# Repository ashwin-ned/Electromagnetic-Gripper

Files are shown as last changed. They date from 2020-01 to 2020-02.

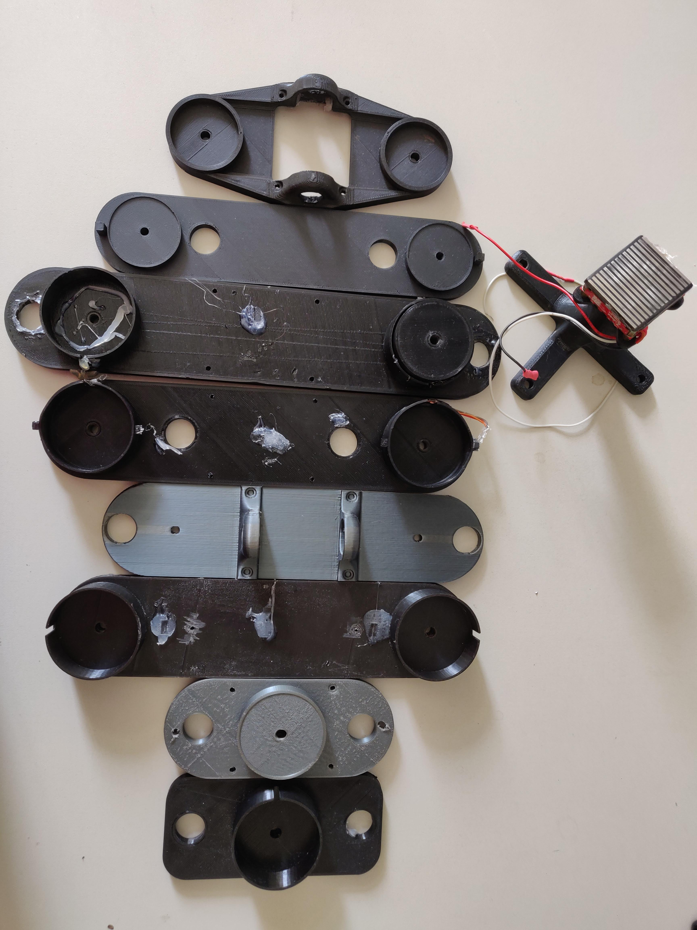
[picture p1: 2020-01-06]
videos/supplementry_media/B.Pictures/Tested_designs.jpg

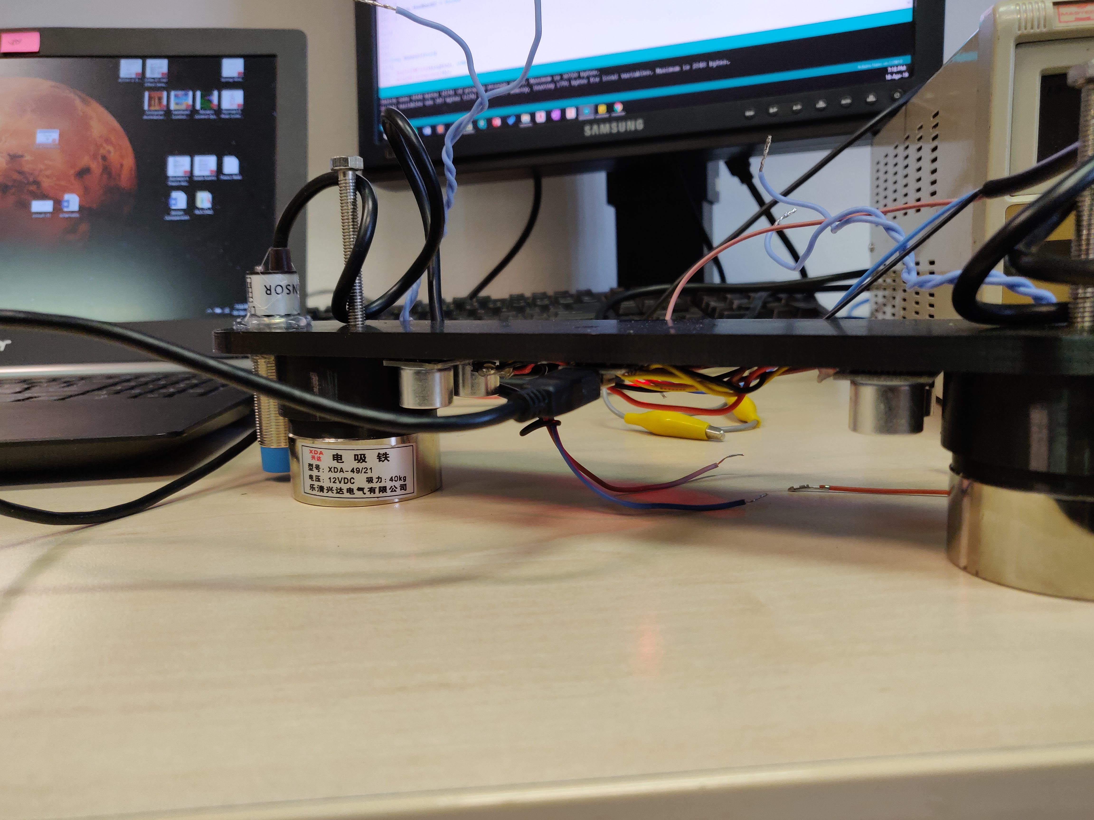
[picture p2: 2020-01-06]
videos/supplementry_media/B.Pictures/Ultrasonic_Test.jpg

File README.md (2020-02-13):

# Design of an Electromagnetic Gripper for Unmanned Aerial Vehicles (UAVs)
Source codes and media files from bachelor's thesis assignment **Design of an Electromagnetic Gripper for Unmanned Aerial Vehicles** with the Multi-Robot Systems Robotics group at Czech Technical University, Prague 2020. 

Note: The work was also accepted for publication in Springer's Lecture Notes in Computer Science under:
A Nedungadi and M Saska. “Design of an Active-Reliable Grasping Mechanism for Autonomous Unmanned Aerial Vehicles”. In Modelling and Simulation for Autonomous Systems (MESAS 2019). 

**Author = Ashwin Suresh Nedungadi** 

**Supervisor = Dr. Martin Saska, Ing.** 

**Website: http://mrs.felk.cvut.cz/**

**Year = 2020** 

**Thesis Topic = Design of an Electromagnetic Gripper for Unmanned Aerial Vehicles**

**Program = Bachelor's in Electrical Engineering & Computer Science [BEECS]**

**ABSTRACT**

This thesis work deals with the design of a grasping mechanism for
aerial grasping and assembly tasks by autonomous unmanned aerial
vehicles (UAVs). The proposed design is aimed at solving ferromagnetic
grasping by UAVs and has onboard sensors that detect and provide
reliable feedback to the UAV. The main focus of the work deals with
the design of the gripper, the technique used for feedback estimation and the integration of the entire mechanism into the current UAV systems at the MRS lab. Furthermore, an overview of the entire system and its implementation are discussed. The developed mechanism is tested multiple times under indoor and outdoor conditions and is designed to be deployed for Challenge II of the MBZIRC 2020 robotics competition in Abu Dhabi.

**Keywords:** unmanned aerial vehicle, aerial grasping, aerial object manipulation, sensor feedback

**Video of Experiments:**

Autonomous grasping test: https://youtu.be/WBgUNp1UqlA

Piloted grasping test: https://youtu.be/bOQ2FRhOzXw

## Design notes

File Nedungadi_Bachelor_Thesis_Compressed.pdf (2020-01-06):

## CZECH TECHNICAL UNIVERSITY IN PRAGUE

## Faculty of Electrical Engineering

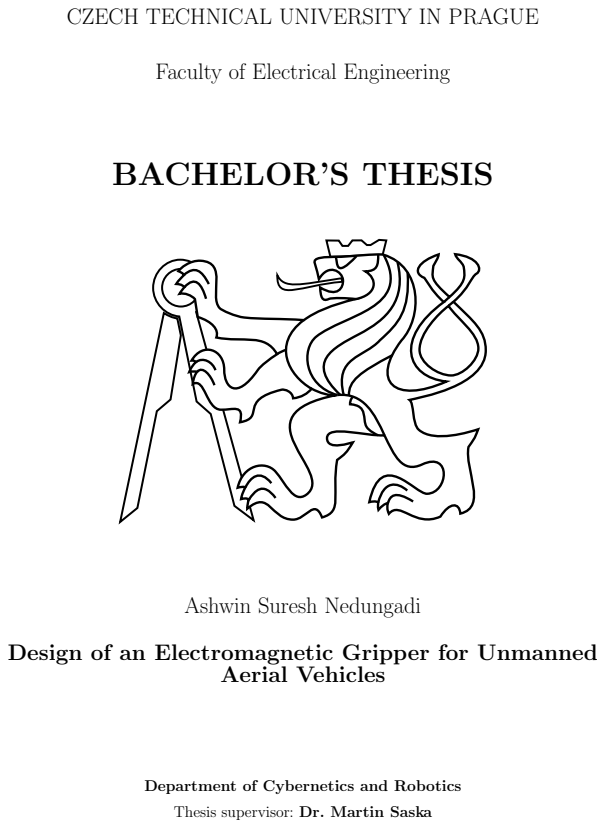
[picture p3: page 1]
BACHELOR’S THESIS; Aerial Vehicles

Ashwin Suresh Nedungadi

Design of an Electromagnetic Gripper for Unmanned

Department of Cybernetics and Robotics
Thesis supervisor: Dr. Martin Saska

# BACHELOR‘S THESIS ASSIGNMENT

I. Personal and study details
Student's name: | Nedungadi Ashwin Suresh | Personal ID number: | 464315
Faculty / Institute: | Faculty of Electrical Engineering

Department / Institute: Department of Cybernetics

Study program: Electrical Engineering and Computer Science

II. Bachelor’s thesis details

Bachelor’s thesis title in English:

Design of an electromagnetic gripper for unmanned aerial vehicles

Bachelor’s thesis title in Czech:

Návrh elektromagnetického uchytovače pro bezpilotní helikoptéry

Guidelines:

The goal of the thesis is to design, implement and experimentally verify a magnetic gripper for construction of a wall by unmanned aerial vehicles (UAV). The task is motivated by the second challenge of the MBZIRC 2020 competition, https://www.mbzirc.com/challenge/2020.
1) Design the magnetic gripper and measure its performance with real test bricks for the MBZIRC Competition.
2) Design and experimentally verify a feedback system for the magnetic gripper using range finder and/or Hall sensors.
3) Develop and Integrate a feedback system, then estimate the feedback status through ROS into the system of Multi-Robot Systems group at CTU.
4) Testing and evaluation of the gripper in the laboratory and field testing with the complete system onboard the drone.

Bibliography / sources:

[1] V Spurny, T Baca, M Saska, R Penicka, T Krajnik, J Thomas, D Thakur, G Loianno and V Kumar. Cooperative Autonomous Search, Grasping and Delivering in a Treasure Hunt Scenario by a Team of UAVs. Accepted in Journal of Field Robotics, 2018.
[2] LaValle, S. M.. Planning Algorithms. Cambridge University Press, Cambridge, U.K., 2006.

Name and workplace of bachelor’s thesis supervisor:

Ing. Martin Saska, Dr. rer. nat., Multi-robot Systems, FEE

Name and workplace of second bachelor’s thesis supervisor or consultant:

Date of bachelor’s thesis assignment: __________ Deadline for bachelor thesis submission: __________

Assignment valid until:
by the end of summer semester 2019/2020
___________________________ | ___________________________ | ___________________________ prof. Ing. Pavel Ripka, CSc. Dean’s signature
doc. Ing. Tomáš Svoboda, Ph.D.
Head of department’s signature

Ing. Martin Saska, Dr. rer. nat.
Supervisor’s signature

III. Assignment receipt

The student acknowledges that the bachelor’s thesis is an individual work. The student must produce his thesis without the assistance of others,
with the exception of provided consultations. Within the bachelor’s thesis, the author must state the names of consultants and include a list of references.
Date of assignment receipt | Student’s signature
CVUT-CZ-ZBP-2015.1 | © ČVUT v Praze, Design: ČVUT v Praze, VIC

i

## Declaration of Independent Work

I declare that the presented work was done independently and that I have listed all sources of information used within it in accordance with the methodical instructions for observing the ethical principles in the preparation of an university thesis.

In Prague on | | |

ii

# Acknowledgements

I would like to thank my supervisor Dr. Martin Saska for his support and guidance during this project. I would also like to thank my advisor Ing. Daniel Heˇrt for his valuable inputs and for teaching me something about hardware. Furthermore, I would like to thank all the members of the Multi-Robot Systems group for their help with the outdoor experiments and for letting me be part of the team.
Finally, I would like to express my gratitude toward my parents who have shown incredible support, love, and encouragement during my studies.

iv

v

### Abstract

This thesis work deals with the design of a grasping mechanism for aerial grasping and assembly tasks by autonomous unmanned aerial vehicles (UAVs). The proposed design is aimed at solving ferromagnetic grasping by UAVs and has onboard sensors that detect and provide reliable feedback to the UAV. The main focus of the work deals with the design of the gripper, the technique used for feedback estimation and the integration of the entire mechanism into the current UAV systems at the MRS lab. Furthermore, an overview of the entire system and its implementation are discussed. The developed mechanism is tested multiple times under indoor and outdoor conditions and is designed to be deployed for Challenge II of the MBZIRC 2020 robotics competition in Abu Dhabi.

Keywords: unmanned aerial vehicle, aerial grasping, aerial object manipulation, sensor feedback

vi

# Contents

List of Figures | ix
List of Tables | xi
1 Introduction | 1
2 Preliminaries | 9
3 Description of the Gripper | 19

viii | Contents
4 Feedback and Control | 31
5 Outdoor Experiments | 43
6 Conclusion | 51
Bibliography | 53
Appendices | 59
Appendix List of abbreviations | 63

# List of Figures

1.1 Example of a UAV with onboard instruments, GPS antenna and battery . 2

1.2 A UAV attempts to grasp a dynamically moving item on top of a turtle bot while another UAV transports the already grasped item to the drop zone
(MBZRIC 2017) | | 4
2.1 Diagram of how communication between nodes work in ROS | | 10
2.2 The variation of magnetic field and flux with thickness of surface | | 12
2.3 Working principle of an ultrasonic sensor | | 13
2.4 Working principle of an inductive proximity sensor | | 14
2.5 Working principle of a hall-effect sensor | | 14
2.6 Free body diagram of UAV with coupled payload | | 15
2.7 Forces acting on a UAV in forward flight | | 16
2.8 Manufactured test bricks | | 17
3.1 Gripper used for MBZRIC 2017 | | 21
3.2 Gripper prototype with ultrasonic sensors and onboard MCU | | 22
3.3 The dual-grasping gripper during test flight | | 22
3.4 Experimental manual flights with onboard gripper prototype | | 23
3.5 Prototype of the rigid gripper with embedded hall-sensors and MCU . . . . | 24

3.6 Modeled CAD assembly of proposed gripper showing 1. Electromagnet, 2.
Gripper housing, 3. Sensors used for feedback, 4. Arduino MCU | | 25
3.7 Modules of the gripper | | 27
3.8 All mechanical components of the gripper | | 28
3.9 Comparison between the previous gripper and proposed gripper | | 29
3.10 Side by side comparison of the grippers in outdoor test flights | | 30

x | List of Figures
4.1 HC-SR04 ultrasonic sensor | | 32
4.2 Feedback algorithm using ultrasonic sensors | | 33
4.3 Unfiltered distance data from ultrasonic sensor during test flight | | 34
4.4 Median filtered distance data from ultrasonic sensor during test flight . . . | 34
4.5 Hall sensors embedded in the electromagnet surface | | 35
4.6 The used inductive proximity sensor | | 36
4.7 Raw data from Hall-Effect sensor and feedback during test flight | | 37
4.8 Raw data from Inductive proximity sensor and feedback during test flight . | 37

4.9 Combined data from proximity & hall sensor and feedback during test flight 38

4.10 Algorithm running onboard the MCU and high level processes | | 39
4.11 Electrical schematic of the gripper circuit | | 40
4.12 Description of the serial protocol | | 41
5.1 Hardware architecture | | 44
5.2 Overview of software pipeline | | 45
5.3 Sub-Pipeline for autonomous grasping | | 46
5.4 The complete system in action during outdoor experimental flights | | 47

5.5 Snaps from outdoor experiments where the complete system is tested under
the challenge II scenario | | 49
5.6 UAV positional control during grasping of brick | | 50
5.7 Control error during grasping of brick | | 50

# List of Tables

2.1 Parameters of tested bricks | | 17
3.1 Comparison between the tested gripping systems | | 29
4.1 Serial bits and their function in used protocol | | 42
4.2 Implemented functions facilitated by ROS | | 42
5.1 Test of maximum slide force | | 48
1 | CD Content | | 61
2 | Lists of abbreviations | | 63

xii | List of Tables

# Chapter 1

# Introduction

### Contents

Unmanned aerial vehicles (UAVs) or Multi-Rotor Systems (Fig. 1.1) that are capable of vertical take-off and landing (VTOL) have undergone a revolutionary advancement in the past few years. They are being used for a wide range of applications in the consumer and technological sector from film making and photography, transportation [1][2][3] and autonomous delivery, hobby products and hobby flying to military applications [4][5] such as defense and reconnaissance systems. UAVs, with on board equipment are also ideal platforms for research [6][7][8] particularly in the areas of disaster relief, search and rescue as well as exploration [9][10] due to their low cost, small size and the variety of configurations in which they can be built.

These vehicles typically consist of 4 (quad-copters) or more rotors with fixed pitch propellers that are driven by brushless DC motors which together, produce thrust for the aircraft. By varying the thrust generated by the individual motors using ESCs (electronic speed controllers), the UAV can pitch, roll and yaw in a given direction.

With the improvement of hardware technologies and their growing applications, UAVs are being used in more complex tasks where interaction and manipulation with the environment are necessary, thus creating an increasing demand for the development of grasping mechanisms that can reliably lift, transport and manipulate objects.

### 2 Chapter 1. Introduction

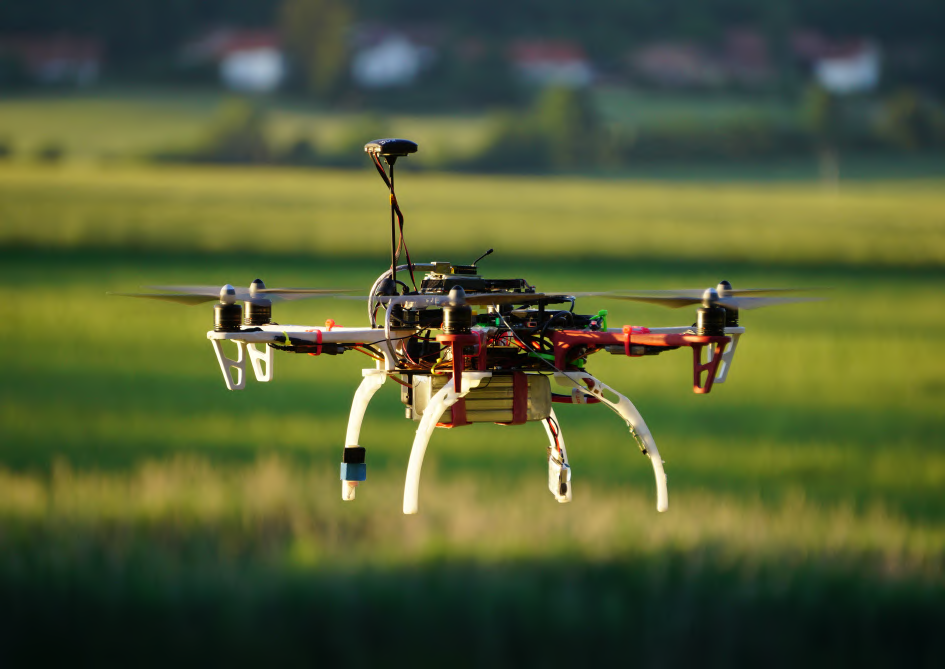
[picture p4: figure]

Figure 1.1: Example of a UAV with onboard instruments, GPS antenna and battery

There are however, many challenges in such aerial grasping tasks as rotor aircraft are inherently susceptible to strong gusts of wind and disturbances during hover making the control of such UAVs a challenge. Other problems include limited payload capabilities of the UAV itself and flight stability with payload coupling as the attached payload changes the flight dynamics compared to free flight.
Moreover, the grasped object should be aligned with the center of mass of the UAV without which, the stability of the UAV is uncertain during transportation of the payload which may induce abnormal maneuvers or oscillations to the UAV, resulting in a crash.

The required grippers for such aerial tasks have to be robust mechanically and must be able to be controlled reliably by a pilot or the autonomous system onboard. They should also stay light-weight and draw the minimum power from the UAV’s battery source to be used in practice.
For aerial grasping or autonomous transportation tasks, the designed gripper must be able to lift a variety of payloads and also be able to provide reliable feedback on the status of the said payload under outdoor conditions.
This thesis deals with the design and verification of a robust electromagnetic based grasping mechanism with a system for reliable feedback of the grasped object for autonomous aerial grasping and manipulation tasks for the upcoming MBZIRC 2020 robotics competition (Sec. 1.3.1).
The thesis work takes an iterative R&D approach, testing and refining various designs over multiple iterations. The design of the grasping mechanism, the approach used to estimate feedback using various sensors and the overall system is described in the following pages.

1.1. Problem statement | 3

## 1.1 Problem statement

The primary objective of this thesis is to design and experimentally verify an electromagnetic grasping mechanism with suitable feedback to be used in an assembly task by a group of UAVs using a range of bricks with different masses and sizes and deploy it for the second challenge of the MBZIRC 2020 competition.
The designed gripper system is then integrated within the UAV system with control and feedback in ROS (Robot operating system). Furthermore, we provide an overall description of the current systems in development for the MBZIRC 2020 competition along with the analysis of the data from the designed gripper during different outdoor experimental tests.

## 1.2 Structure of this thesis and contribution

This thesis work is structured into 6 main chapters as follows:

- The first chapter gives an introduction to the problem, the challenge and source of inspiration and also discusses related works in detail. Most of the cited research works focus on the topics related to the theme of this thesis.
- In the second chapter we establish some preliminary conditions and discuss various principles necessary to fully understand the problem and solution design.
- In chapters 3 and 4, we provide the description and design of the proposed grasping mechanism, the algorithms and also include certain high level and low level aspects of the system.
- In chapter 5 we present the description of the overall UAV system as well as experimental data from test flights followed by some analysis and discussion of the experiments, and in chapter 6 finally we conclude the work.

This thesis contributes directly to the research done for the MBZIRC project where we present [11] a novel idea for an electromagnetic grasping mechanism that can lift theoretical payloads of up-to 6 kg. The designed gripper is robust and can lift a range of ferromagnetic payloads from small loads of 100 g to 6 kg. The designed gripper is thoroughly tested in multiple outdoor experiments and through iterative design refined into a final prototype to be used for the competition.

### 4 Chapter 1. Introduction

## 1.3 MBZIRC competition

The Mohamed Bin Zayed International Robotics Challenge (MBZIRC) [12] is an international robotics competition that is held every two years in Abu Dhabi, United Arab Emirates and comprises of various demanding challenges in which the best university teams in the world compete in attempts to solve the challenges (Fig. 1.2) for maximum amount of points.

The objective of the MBZIRC competition is to provide an ambitious and technologically demanding set of challenges in robotics intended to demonstrate the current state of the art in robotics in terms of scientific and technological accomplishments, and to inspire the future of robotics.

In the MBZIRC 2017 competition, the team led by Multi-Robot Systems group from Czech Technical University won various prizes in the different challenges presented. The team comprised of 20 members as a part of a larger collaboration effort between the University of Pennsylvania, University of Lincoln.
The most notable and relevant prize won by the team to this thesis was the first place in the third challenge where a group of 3 UAVs had to locate and retrieve circular metallic disks and drop them in a defined drop zone in a “Treasure Hunt” scenario. This thesis builds upon the lessons learnt from the MBZIRC 2017 experience and contributes towards the upcoming MBZRIC 2020 competition.

Figure 1.2: A UAV attempts to grasp a dynamically moving item on top of a turtle bot while another UAV transports the already grasped item to the drop zone (MBZRIC 2017)

1.4. State of the art | 5

### 1.3.1 MBZIRC 2020

The next MBZIRC competition is scheduled for February of 2020 in Abu Dhabi with over 30 international teams competing for the prizes. MBZIRC 2020 will be based on autonomous aerial and ground robots, carrying out navigation and manipulation tasks under harsh indoor and outdoor conditions.
MBZIRC 2020 will consist of three individual challenges and a triathlon type Grand Challenge which is a combination of the first three challenges. The challenges will be focused in the areas of UAV tracking & interaction, construction automation and urban fire-fighting:
- In challenge I, the first task requires a team of UAVs to autonomously detect, track and eliminate a set of balloons in an open field, the second task requires a UAV to chase and catch a ball that is being transported by another UAV. Challenge I is motivated by precise detection and elimination tasks by UAVs and UAV safety.
- In challenge II, a team of 3 UAVs along with a UGV (unmanned ground vehicle) detect, grasp, transport and assemble different types of bricks into a pre-defined structure in an outdoor environment. This challenge is motivated by autonomous construction using robots.
- In challenge III, the same team comprising of 3 UAVs and a UGV is required to work cooperatively to extinguish a series of simulated fires in a building structure under an urban fire-fighting scenario.
- In the final Grand Challenge, the team of autonomous robots work together to attempt to solve all the 3 challenges simultaneously in a timed event.

## 1.4 State of the art

There are several available solutions for aerial grasping. Many of which focus on passive magnetic grasping and robotic claw like manipulators for the grasping or aerial manipulation of objects. We will discuss each of the various techniques proposed and their advantages and disadvantages for aerial grasping tasks.

One such example of a solution for aerial grasping includes work done by the RISC laboratory at King Abdullah university of science and technology [13] where a passive magnetic gripper with an impulse release mechanism and push-button feedback was developed. The design uses 16 small neodymium magnets which together produce the required magnetic force to grasp a ferromagnetic object. The release of the grasped object is facilitated by two high speed servos which pushes the drop plate and produces a high impulse release of the object.
While this kind of grasping mechanism provides a low-power passive solution, the grasping

### 6 Chapter 1. Introduction

capabilities provided by permanent magnets are inferior compared to that of an electromagnet in terms of magnetic strength and control. Furthermore, the release mechanism that relies on servomotors to separate the grasped object with impulse is bulky and adds another layer of unnecessary complexity to the system.
A scaled up version of this concept was also developed by the KAIST team [14] for MBZIRC 2017 competition. The system integrated contact sensors and 2 camera modules on the gripper for visual servoing and used 13 neodymium magnets and 4 servomotors that actuated the drop plate to forcefully separate the grasped object from the gripper.

Another popular solution for magnetic grasping utilizes electro-permanant magnets (EPMs) due to their low-power consumption (table 3.1), payload capabilities and ability to toggle the magnetic strength by magnetizing and demagnetizing the EPM with the help of an active external switching circuit.
This solution was used by several teams, including our own team in the 2017 MBZRIC competition using the COTS¹ OpenGrab EPM V3 from nicadrone [15][16][17].
A custom EPM based solution was also presented in the work [18] by ETH Zurich which has the ability to grasp ferromagnetic objects with a curvature of up to 30 degrees and utilizes alnico and neodymium magnets. Another custom solution was tested in the MRS lab for cooperative grasping by UAVs in the master’s thesis work [19] which used servomotors to rotate neodymium magnets by 90 degrees for grasp and release.
Although electro-permanent solutions are popular candidates for aerial grasping and manipulation tasks and offer low-power solutions, they come with many disadvantages. They are expensive, do not scale well with mass, have low payload capabilities and require an active control circuit to magnetize and demagnetize the magnet. Furthermore, there is a need for firm contact with the ferrous surface in order to grasp the object successfully. Moreover, as experienced by our team [16] and other teams [15][17] during the last MBZIRC 2017 competition, the magnet can also break if used with heavy force and the circuitry can burn out if the command signal is sent multiple times resulting in many gripper failures and an overall low success rate [17]. The teams also found that the EPM solution provided to be too weak in outdoor conditions where gripper failure was even caused due to the thick layer of paint on the objects in the competition [15][16][17].

There exists several unique ideas for aerial grasping developed over the years such as impactive or claw based, ingressive grasping techniques and suction based grasping. Impactive grasping mechanisms that are modeled after claws or human arms are widely studied problems in robotics. They are also used by industrial robots as end effectors for various automation tasks. Over the years there have been several publications regarding these mechanisms[20][21][22] each optimized for a specific task with it’s own set of advantages and disadvantages. Although such mechanisms offer a robust solution to grasp a wide range of objects with different shapes, they are far too complex and heavy to be used onboard UAVs. However, there are many existing simplified grasping mechanisms [23][21]

1Commercial off-the-shelf

1.4. State of the art | 7

and they have been proven to be suitable for grasping of wooden blocks and packages. But considering the requirements for the MBZIRC 2020 competition and the engineering complexity of developing such a mechanism, we had to eliminate such grasping techniques. Moreover, under a competitive scenario it is crucial that the hardware engineers are able to quickly debug and resolve any issues that could arise and having a complex system onboard multiple UAVs would be more of a liability to our team than a strength.

Two unique solutions for aerial grasping are presented in the works [24][25]. The first being a self-healing suction mechanism that utilizes an onboard vacuum pump that produces the sufficient volume flow to grasp a variety of payloads. Although the possibility of using suction for aerial grasping proves to be a great solution for non-magnetic object grasping and grasping of items with small curvature, the disadvantage of having a big enough compressor for heavy payloads and sufficient volume flow onboard the UAV combined with its complexity made it a clearly unsuitable candidate for our task.
The other grasping mechanism for aerial grasping utilizes an ingressive gripper. The mechanism consists of metallic “claws” or “hooks” driven by servo motors which penetrate the surface of the object to be grasped and hooks itself into the surface, allowing the UAV to carry the object. The hooks are then retracted using the servo motors when the UAV needs to release the object.
Such a mechanism is very useful as demonstrated in the work [25], to transport wooden blocks or packages with strong cardboard linings. However, it is impractical when it comes to rigid or delicate objects as it relies on penetrating the surface to grasp and makes an indent in the process which in the long term proves to be impractical and especially unsuitable for our task as the objects we want to grasp will be metal.

While the above mentioned aerial grasping solutions are not as simple or heavy payload compatible, our solution is designed for ferrous payloads and provides reliable feedback using multiple sensors on whether an object is successfully grasped or not. Moreover, electromagnets provide the solid advantage of scalability to the system while being cheap and can be hot swapped on the field to accommodate heavier or lighter payloads or in case of failure. The mechanical design of our gripper is developed with reliability and operation in outdoor desert conditions in mind while being able to lift ferrous objects weighing theoretically up to 6 kg with the only limitation being the payload capacity of the UAV used.

### 8 Chapter 1. Introduction

# Chapter 2

# Preliminaries

### Contents

In order to proceed with the rest of the thesis work, we need to establish some knowledge of the working principles involved. This chapter gives a brief introduction to the physical concepts and theory involved.

## 2.1 Robot Operating System (ROS)

ROS [26] is an open-source, meta operating-system running on Unix-based platforms and is widely used by the robotics community.

It provides the services expected from an operating system, including hardware abstraction, low-level device control, implementation of commonly-used functionality, message-passing between processes, and package management. It also provides various tools and libraries for obtaining, building, writing, and running code across multiple computers.
The basis of ROS is made up of packages, where all the software are located in the form of executable and supporting files.

A node in ROS is a process that performs some computation. Nodes in ROS can receive or publish messages known as “topics” to other nodes in a distributed manner. A robotic

### 10 Chapter 2. Preliminaries

system usually comprises of many nodes each of which does a specific task. For example, one node controls a laser range-finder, one node controls the thrust inputs to a controller, one node performs path planning, one node publishes diagnostics about a running process, and so on. Nodes can also call upon other nodes to do a specific task in the form of ROS services. ROS services are bi-directional messages and expect a reply from the receiving end.

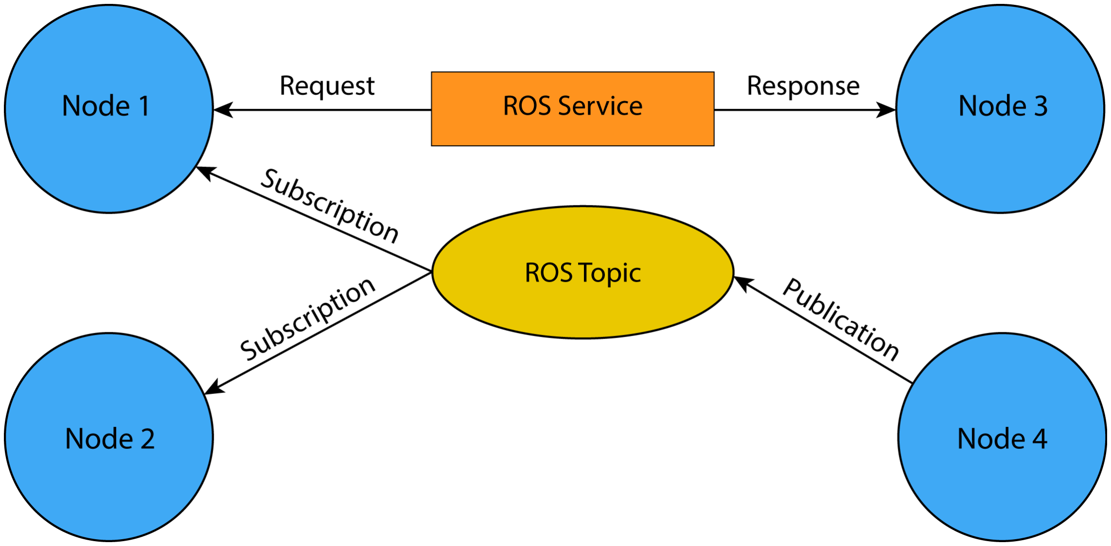
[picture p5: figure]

Figure 2.1: Diagram of how communication between nodes work in ROS

A ROS distribution is a versioned set of ROS packages. These are akin to Linux distributions (e.g. Ubuntu). The purpose of the ROS distributions is to let developers work against a relatively stable codebase until they are ready to roll everything forward.
Various distributions of ROS are used in the robotics community, the latest being Lunar Loggerhead. We however use Melodic Morenia for the purpose of our tasks.

## 2.2 Concepts of Electromagnetism

An electromagnet is a device consisting of a core of soft magnetic material¹
surrounded by
a coil through which an electric current is passed to magnetize the core. By definition, this means that an electromagnet can be turned on and off by passing current through it’s coil making it highly suitable for a wide range of applications.

Engineering an electromagnet is systematized by known equations that characterize a magnetic circuit and which decide certain properties of the designed electromagnet such

1Soft magnetic materials are those materials that are easily magnetised and demagnetised. They do not retain their magnetism after the electric current is removed.

2.2. Concepts of Electromagnetism | 11

as holding force.
The holding force of an electromagnet is defined as the force which is perpendicular to the attraction surface of the holding magnet.
The force exerted by a magnetic field or the holding force of an electromagnet is described by the equation:

Fh =

B²A
2µo
, | (2.1)

for a closed magnetic circuit with no air gap:

B =

NIµ
L
. | (2.2)

Where B is the magnetic flux density; A is the cross sectional area of the core; N is the number of turns of coil winding; I the current in the winding coil and L, the length of the magnetic field path.
The constants µ and µo being the permeability of the electromagnet core material and permeability of free space respectively.

Substituting (Eq. 2.2) into (Eq. 2.1), we get the relationship for the holding force of an electromagnet:

Fh =

N²
I

2µ

2A
2µoL²
. | (2.3)

Electromagnets are also subject to side effects, some of which that must be discussed here as they will become relevant later [27][28][29].

1. Power losses due to Ohmic heating: In electromagnets, it is common for energy to dissipate as heat due to the resistance of the windings which scales proportionally as the size of the electromagnet begins to increase.
Electromagnets come in various thermal insulation classes, which is categorized by a limiting temperature beyond which the performance of the electromagnet will be affected²
The ohmic heating effect can be reduced by limiting the current in the coils or using thicker coils to decrease their resistance.
2. Inductive voltage spikes during disconnection: Electromagnets have significant inductance which resists changes in the current through its windings, sudden changes in the winding current causes large voltage spikes across the windings.
This is because when the current through the magnet is increased, such as when it is turned on, energy from the circuit is stored in the magnetic field. When it is turned off the energy in the field is returned to the circuit. Thus, when an electromagnet is disconnected, the energy in the magnetic field is suddenly returned to the circuit, causing a large voltage spike and an arc across the switch contacts. The electrical

2The magnet used in this project has an insulation class of B (130⁰ C)

### 12 Chapter 2. Preliminaries

circuits involving electromagnets usually counter this problem with the help of a “freewheeling diode” or “fly back diode” [30] connected across the electromagnet. Large electromagnets avoid this by using power circuits controlled by a microprocessor that achieves current changes slowly, in gentle ramps taking several minutes to energize or deenergize the magnet.

3. Remanence effect: Remanence or residual magnetic field [31][32] is the magnetization left behind in a ferromagnetic material after the external magnetizing field is removed. This effect is known to occur in electromagnets causing the payload to be attached to it even after the electromagnet has been turned off. This problem can be countered by a process known as degaussing or in our case, a quick polarity change of the electromagnet voltage.
4. Variation of holding force as a function of surface thickness: From our earlier equation (Eq. 2.1), the holding force of a magnet is characterized by the square of it’s flux density [33]. Hence, the holding force of an electromagnet relies on the thickness of the part to be held.
The thicker the target surface is, the greater the number of magnetic field lines passing through the object (Fig. 2.2 from [28]). Therefore, if the part to be held is too thin then it will not be able to accommodate all the available field lines and will become saturated. The force will then be inadequate and the electromagnet will be unable to hold on to such a thin surface.

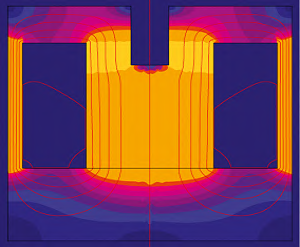
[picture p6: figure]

(a) Surface of thickness 0.2 mm | (b) Surface of thickness 10 mm

Figure 2.2: The variation of magnetic field and flux with thickness of surface

2.3. Sensors used and working principles | 13

## 2.3 Sensors used and working principles

A few different types of sensors were considered for the feedback of whether a brick was successfully grasped or not as this was a critical task for autonomous grasping. We will look into the principles of their working.

### Distance Sensing with Ultrasonic Sensor

Ultrasonic sensors work by emitting sound waves at a high frequency then wait for the sound to be reflected back, calculating distance based on the total time (Fig. 2.3 from [34]). This is similar to how radar measures the time it takes a radio wave to return after hitting an object. For this reason an ultrasonic sensor has an ultrasonic emitter and receiver.
We know the elementary formula Distance = Speed ∗ T ime, thus by measuring the time taken by an ultrasonic wave to be reflected off an object and detected up the sensor again, we can formulate:
d = c.

1
2
t | (2.4)

where d is distance and is given by the product of c - speed of sound in air at room temperature (≈ 343 m/s) and t - the total transmission time.

Figure 2.3: Working principle of an ultrasonic sensor

### Distance Sensing with Inductive Proximity Sensor

Inductive proximity sensors are non-contact measurement devices used in detection of metallic objects. Their operating principle is based on a coil and oscillator that creates an oscillating electromagnetic field in the close surroundings of the sensing surface (Fig. 2.4 from [35]). The presence of a metallic object in the operating area causes a dampening of the oscillation amplitude due to energy loss by induced eddy currents in the metallic object.
The rise or fall of such oscillation is identified by a threshold circuit that changes the output of the sensor. In the sensor used for this thesis³
, this threshold was at 2 mm distance from the sensor.

3The sensor used is the LJ8A3-2-Z Inductive Proximity Sensor with sensing capability of upto 2 mm.

### 14 Chapter 2. Preliminaries

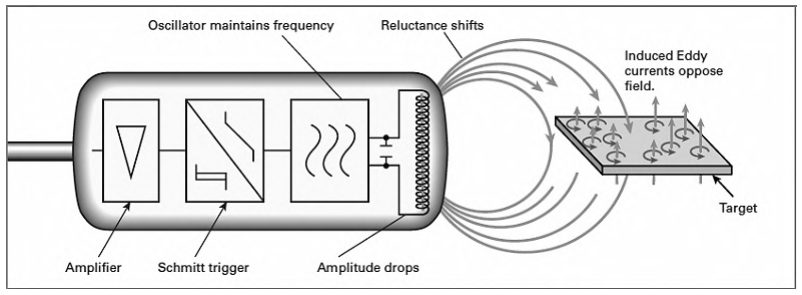
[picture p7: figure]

Figure 2.4: Working principle of an inductive proximity sensor

### Magnetic Sensing with Hall-Effect Sensor

A Hall effect sensor is a device that is used to measure the magnitude of a magnetic field (Fig. 2.5 from [36]). Its output voltage is directly proportional to the magnetic field strength through it.
Hall effect⁴
sensors are used in various areas to measure position, speed, and magnetic field. The principle of semiconductor hall sensors is that when a current-carrying semiconductor is introduced to a magnetic field, the charge carriers of the semiconductor experience a force in a direction perpendicular to both the magnetic field and the current⁵ and hence a voltage appears at the semiconductor edges.

Figure 2.5: Working principle of a hall-effect sensor

4The sensor used is a linear hall effect sensor SS49e 5As per Fleming’s right hand rule

2.4. Forces acting on a UAV with coupled payload | 15

## 2.4 Forces acting on a UAV with coupled payload

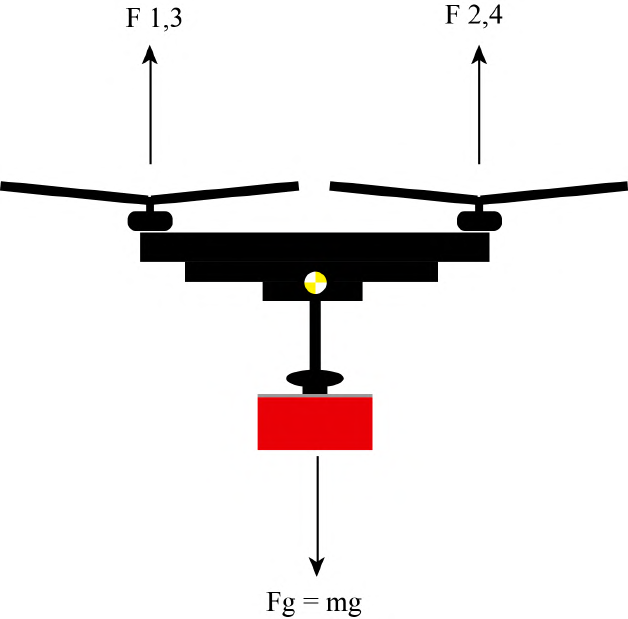
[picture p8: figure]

Figure 2.6: Free body diagram of UAV with coupled payload

The forces acting on the UAV [37] behaves differently based on if a payload is attached rigidly or can move about some axes. In the case of rigid mechanics, There is a force acting downward (Fig. 2.6) F~
g = m~g which needs to be compensated by the collective thrust produced by the UAV F~

c = F~

1 + F~

2 + F~

3 + F~

4. The thrust force F~
i of a rotor can be given
by the formula:
F~
i = Kf ω

2
(2.5)

Where ω is the rate of rotation of the propellers and Kf is a proportionality constant that depends upon many factors like torque proportionality constant, back-EMF, Density of surrounding air, area swept by propeller etc. and is measured empirically.
At equilibrium (hover condition), the collective thrust generated by a quadrotor balances out the weight of the drone as:

X

4

i=1

Kf ωi

2 + m~g = 0 | (2.6)

But suppose the thrust is more than the mass, in this case the quadrotor accelerates upward and the equation is given by:

X

4

i=1

Kf ωi

2 + m~g = m~a | (2.7)

### 16 Chapter 2. Preliminaries

Figure 2.7: Forces acting on a UAV in forward flight

A UAV in flight, is acted upon by four basic aerodynamic (Fig. 2.7) forces [38]:

1. Lift: Lift is the force that opposes the downward force of weight and is produced as a result of the motion of the propellers through air [39]. It depends on factors such as speed of airflow, density of air, area and pitch of the used propellers. For a quad-copter, the maximum lift produced is fixed due to the fixed pitch propellers and maximum rpm (revolutions per minute) generated by each motor.
2. Weight: Weight is the combined load of the UAV itself, including the instruments, air-frame, payload and battery. It pulls the UAV downward due to the force of gravity and opposes lift vertically in the opposite direction through the center of gravity. In most cases, the weight of the UAV is fixed and known.
3. Thrust: The force produced by the rotors is called thrust. It can be forward, rearward, sideways or vertical. The UAV attitude and thrust determines the direction of movement of the UAV.
4. Drag: The drag force is a rearward, retarding force caused by wind resistance and disruption of airflow by the rotor, air-frame and payload. It opposes thrust.

In the case of a coupled payload, a certain degree of freedom can complement the UAV’s ability to carry and transport the payload while reducing mechanical stress and strains on the grasping or suspension mechanism. However, a new problem arises where the disturbances during flight cause the coupled payload to swing around like a pendulum. This problem is widely studied [40][41] but cannot be easily overcome in the real world without the proper position and orientation feedback of the payload and the aerodynamic interactions due to the downward airflow from the UAV.

2.5. Parameters of tested bricks | 17

## 2.5 Parameters of tested bricks

To simulate the correct conditions for our outdoor experiments, it was necessary to manufacture and test our systems on the proposed bricks from the MBZRIC 2020 organizers. A complete list of the challenge criteria and parameters of the objects involved can be found online [12].
The manufactured test bricks used Styrofoam, adhesive and metal sheets of various thick-
ness providing the necessary mass for the proposed bricks⁶ | . Multiple bricks were manufac-
tured with the heaviest variant being 4 kg (blue) and the lightest being 0.75 kg (red). The tested bricks and their parameters are shown in table 2.1.
Brick Color | Dimensions | Mass
Red | 0.30 m x 0.20 m x 0.20 m | 0.75 kg - 1.0 kg
Green | 0.60 m x 0.20 m x 0.20 m | 1.40 kg - 2.0 kg
Blue | 1.20 m x 0.20 m x 0.20 m | 2.36 kg - 4.0 kg

Table 2.1: Parameters of tested bricks

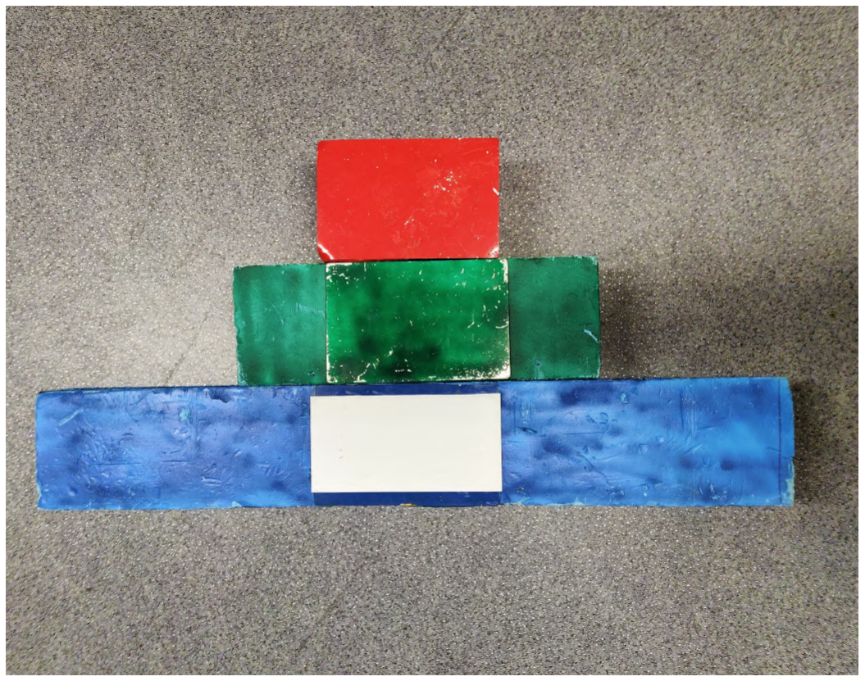
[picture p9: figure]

Figure 2.8: Manufactured test bricks

6The manufactured bricks were made to be worst case scenarios of the described parameters from MBZIRC 2020, hence they exceeded the competition requirements.

### 18 Chapter 2. Preliminaries

# Chapter 3

# Description of the Gripper

### Contents

Aerial grasping and manipulation is a well known problem in the field of modern aerial robotics. They are also highly desirable capabilities that an unmanned aerial vehicle can possess.
In most cases however, commercial based aerial grasping mechanisms such as magnetic or suction-based end effectors designed for industrial robots, are not suitable for autonomous aerial operation or robust enough to be employed so. Therefore, custom designed grasping mechanisms are often favored because the current state of the art in 3D printing technology makes it accessible to rapidly prototype such custom solutions and the fact that they can be customized for specific applications and adapted on the field makes it an ideal choice for research and development.

The designed grippers for aerial manipulation and transportation tasks must be engineered to be mechanically robust and compliant while considering the following requirements:

- Lightweight
- Sufficient holding force for payload
- Low power consumption
- Autonomous control and reliable feedback

### 20 Chapter 3. Description of the Gripper

- Fail-safe grasp and release

A viable aerial grasping mechanism will have to fullfill the above conditions to be used onboard an autonomous UAV in outdoor conditions.

## 3.1 Tested Iterations

Following the methodology for iterative designing, we have tested multiple prototypes for a suitable electromagnetic grasping mechanism while rejecting bad designs and reinforcing promising ones through trial and error.

### EPM based solution

The gripper (Fig. 3.1) used for MBZIRC 2017 [16] consisted of an Electro-Permanent Magnet (EPM) end effector attached to a ball joint that could freely rotate in all directions and a compression spring along the shaft that connects it to the UAV.
Although this worked well for the task described by the competition (Sec. 1.3), several groups who participated (Sec. 1.4) experienced problems with the EPM based solution [15][17] including our team from CTU.

The primary problem was the burning of the control circuit on the OpenGrab V3 EPM when the command signal for activation is sent multiple times as this was done to strengthen the holding force after an object was initially grasped. Secondly, the EPM is very delicate for outdoor environments as dirt or gravel could be crushed into the surface causing an insulation breakdown [42]. Furthermore, it provided to be weak in terms of holding force as it only had 15 kg of holding force which was effectively reduced it to 2.25 kg in shear [16] and even lower considering the forces acting on it during flight [38].

Another problem encountered by our team was due to the design of the mechanical ball joint which had unlimited freedom in the yaw axis, which meant that any object grasped in flight would yaw along the directions of the acting forces and considering that the competition took place near the sea and was affected by strong sea breezes, this became problematic.
Since the next competition requires UAVs to transport long cuboidal bricks, a ball joint would be highly undesirable due to the uncontrollable yawing motion caused by the different forces on the payload in flight [38].
Considering all the above problems it was decided to abandon any EPM based solution for the next MBZIRC as the objects described were bigger and have masses upward of 1 kg.

3.1. Tested Iterations | 21

Figure 3.1: Gripper used for MBZRIC 2017

### Dual electromagnets with ultrasonic-hall feedback

While going through the design process for the gripper, it was crucial to come up with a design that was capable of grasping and transporting the proposed long brick-like objects in challenge II (Sec. 1.3.1).
Our hold force and power requirements were satisfied by a single electromagnet which had dimensions of 49/21 mm and was capable of lifting up to 40 kg under ideal conditions. The problem then is to take into consideration that the longest brick to be grasped was 1.2 m long and weighed 1.5 kg. For such a long brick, the placement of two electromagnets of lifting power 40 kg each separated by a distance of 20 cm was ideal¹ as the gripper would experience fewer torque effects (Fig. 3.3). As the challenge is timed, it is important to transport the bricks as fast as possible without causing disturbances to the payload or UAV. Hence, by grasping the brick at 2 positions, the drone could fly faster safely. The

1The separating distance of 20 cm was chosen as it was the right distance to accommodate even the smallest brick which was 0.3 m long

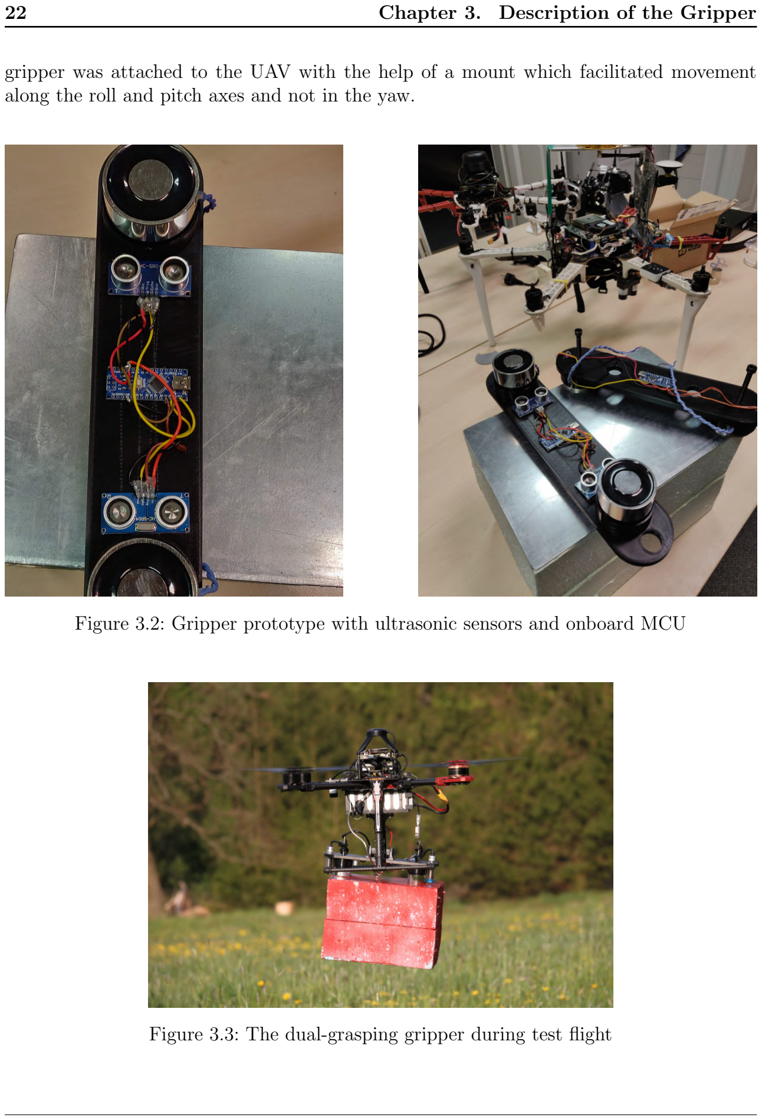
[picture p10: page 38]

### 22 Chapter 3. Description of the Gripper

gripper was attached to the UAV with the help of a mount which facilitated movement along the roll and pitch axes and not in the yaw.

Figure 3.2: Gripper prototype with ultrasonic sensors and onboard MCU

Figure 3.3: The dual-grasping gripper during test flight

3.1. Tested Iterations | 23

During the preliminary tests (Fig. 3.4), three prototypes of the gripper were tested, one with dual ultrasonic feedback (Fig. 3.2); the second with feedback from hall effect sensors: and finally a prototype that combined the ultrasonic sensors with proximity sensors to calculate total feedback of the gripper. The signal processing for feedback from each prototype is discussed in the next chapter.

Although by the design of the 2-DOF mount, the mechanism was able to align the grasped brick to the center of gravity (Fig. 3.3), there was a major drawback with the prototype. The long design of the dual grasping mechanism meant extra unnecessary weight, redundant sensors and twice the power consumption by the two electromagnets which translated to limited operating time before the batteries had to be changed. Moreover, due to the longer design, the gripper exhibited unstable “see-saw” like motion during flight when there was no payload due to the slight variation of forces acting on either ends due to downwash generated by the propellers and wind.
Due to the above reasons and due to the fact that there was a clear trade-off between the electromagnet’s hold force and power consumption, there was a need to simplify and miniaturize the design.

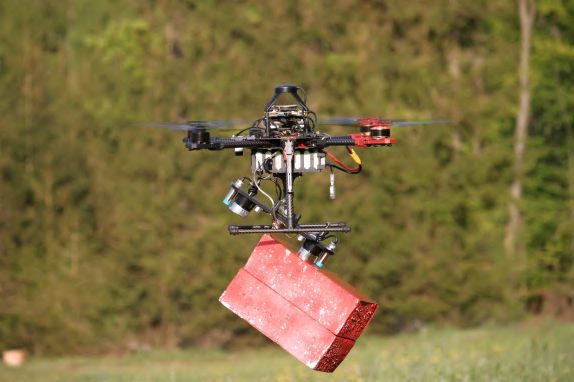
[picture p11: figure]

(a) The UAV in flight without payload | (b) Gripper with partial grasping of brick

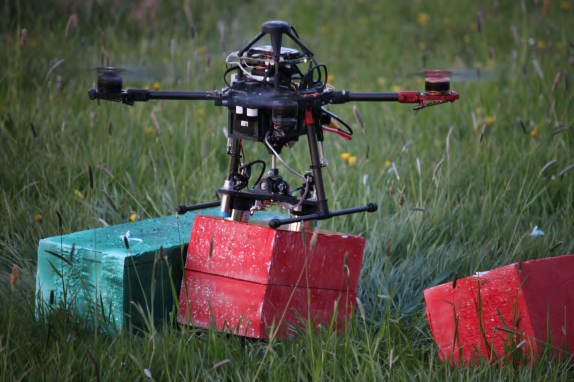
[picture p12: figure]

(c) UAV in front of wall structure | (d) UAV attempts to place a brick

Figure 3.4: Experimental manual flights with onboard gripper prototype

### 24 Chapter 3. Description of the Gripper

### Rigid Gripper

Another prototype proposed and tested by the MRS Lab was the idea of a solid gripper with a linear array of electromagnets that can grasp the brick horizontally. This prototype consisted of two smaller electromagnets of 25 kg holding force each and had hall sensors embedded on their surfaces for feedback. The base would attach via a solid compression shaft that is completely rigid and 3D printed as shown in Fig. 3.5.

While the solid design offers good brick placement for building a wall, such a design is not very robust as the forces during flight will act on the payload coupled UAV and cause high drag and mechanical strain on the gripper itself as well as decrease the hold force of the magnets [16]. To compensate for this, the UAV’s maneuvers and speed have to be severely restricted so that the brick does not fall down during transportation. Moreover, high quality of the 3D print has to be ensured without which, the base would fracture from the shear forces of flight.

(a) Side view showing the MCU, the compression shaft and mounting for the UAV

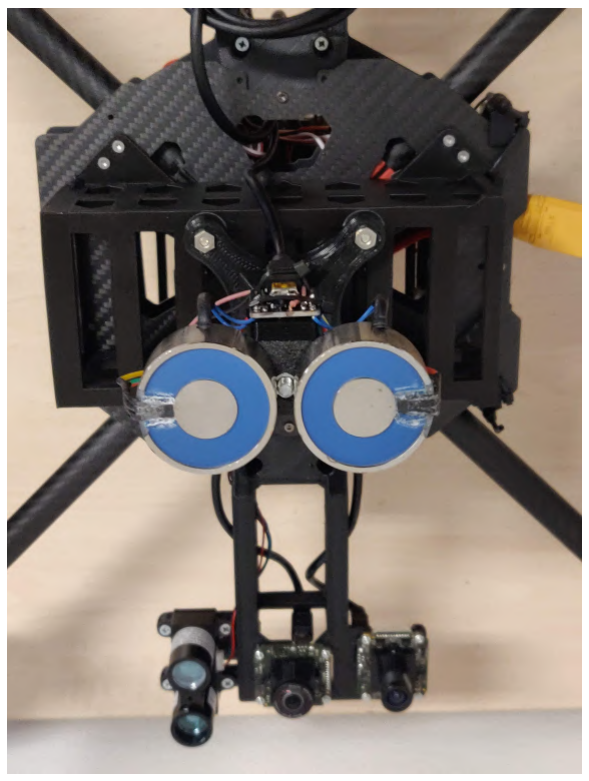
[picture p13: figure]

(b) Bottom view showing the embedded hall sensors on the electromagnet surface

Figure 3.5: Prototype of the rigid gripper with embedded hall-sensors and MCU

3.2. Proposed gripper design | 25

## 3.2 Proposed gripper design

The current proposed design of the gripper consists of 4 major components:

1. An electromagnet with switching circuit
2. Gripper housing with compression shaft and mounting attachment
3. A combination of a hall-effect sensor embedded in the electromagnet and inductive proximity sensor for feedback
4. Arduino MCU that processes raw signals from the sensors, communicates with the on-board computer and also controls the switching circuit of the gripper.

Figure 3.6: Modeled CAD assembly of proposed gripper showing 1. Electromagnet, 2. Gripper housing, 3. Sensors used for feedback, 4. Arduino MCU

### 26 Chapter 3. Description of the Gripper

### Electromagnet and switching circuit

An industrial electromagnet capable of lifting up-to 40 kg of payload provides the necessary magnetic hold force for grasping. The electromagnet is supplied a constant 12 V DC for its operation and has a custom built N-MOSFET switching circuit integrated with the Arduino that can be toggled by the UAV’s onboard computer (Sec. 2.1). Although the electromagnet consumes 10 W, it is insignificant compared to the power drawn by the UAV’s onboard computer (60 W) and motors (1000 W) from the 8000 mAh ( 178 Wh) Li-Po Battery. And considering the magnets won’t be turned on and in operation continuously throughout the flight, there is no particular reason to be concerned by the electromagnet’s power consumption.

### Gripper housing and mount

The gripper base (Fig. 3.7a) and mounting bracket is designed to be sturdy structurally and is fabricated using 3D printing technology with PLA and ABS plastic.
It has 2 degrees of freedom in the pitch and roll axes and consists of a main mount where the sensors, magnet and MCU are fixed, an inner and outer ring structure with ball bearings (Fig. 3.7c) to facilitate the movement along the two described axes and a shaft with a mounting bracket so it can be attached to the UAV with 4 screws and nuts (Fig. 3.7b) (Fig. 3.7d). By the mechanical design of the gripper, the angle of rotation for the 2 axes are restricted to approximately 30 degrees, this ensures that the grasped object does not swing too much and cause a disturbance for the drone.

### Feedback sensors and signal processing

Reliably estimating the status of a successful grasp is a crucial task for aerial autonomous grasping. The gripper integrates feedback from two independent sensors: A hall sensor embedded in the electromagnet’s surface and an inductive proximity sensor mounted on the side. The raw analog signal is first digitized by the Arduino’s 10-bit ADC (analog-digital converter) and is then processed using an algorithm and a final feedback is given using a combination of the feedback from the individual sensors.

The chosen MCU for prototyping the gripper is an Arduino nano as it is low-power (≈ 0.1 W), open-source and easy to program in the Arduino IDE. It also has 8 analog pins with a 10-Bit ADC for acquiring signals as well as 22 digital I/O pins which makes it very convenient to use in rapid prototyping.
The electronic components of the gripper consist of the electromagnet, N-Mosfet, Arduino nano MCU, hall-effect sensor and an inductive sensor.

3.3. Modeling & Assembly | 27

## 3.3 Modeling & Assembly

The gripper was modeled using Autodesk Fusion 360 CAD software and consists of 5 basic 3D printed modules shown in Fig. 3.7:

(a) The gripper base with holes for the proximity sensor and electromagnet with embedded hall sensor

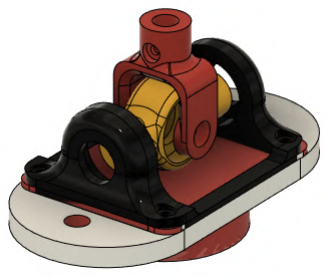
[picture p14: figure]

(b) The mount that connects the upper portion of the gripper with the base (black)
(c) Housing that connects the shaft to the base and housing that accommodates ball bearings and attaches to the gripper and together provides 2-DOF

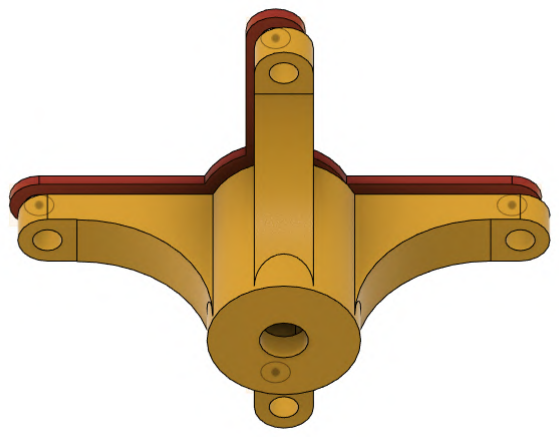
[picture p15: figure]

(d) The mount with spring for dampening and which connects to the UAV

Figure 3.7: Modules of the gripper

### 28 Chapter 3. Description of the Gripper

The gripper has a few components (Sec. 3.2) including sensors and MCU which can be assembled or soldered to each other by hand and assembled together to the 3D printed parts (1-5) by using some screws, nuts and short cylindrical²
inserts (a-g).
All the components and the final assembled product are shown in (3.8)(3.9).

Figure 3.8: All mechanical components of the gripper

2a - ball bearings; b - a metal rod with hex end; c - compression spring; d - cylindrical inserts; e -threaded bolt; f - M6 screw; g - two nuts

3.4. Comparison of tested prototypes | 29

## 3.4 Comparison of tested prototypes

Parameter | EPM Design | Dual Design | Rigid Design | Proposed Design
Weight | 250 g | 580 g | 350 g | 400 g
Max Rated Payload | 15 kg | 80 kg | 50 kg | 40 kg
Max Shear Payload | 2.25 kg | 12 kg | 7.5 kg | 6 kg
Max Tested Payload | 500 g | 1.5 kg | 2.3 kg | 4 kg
Feedback | Single | Multiple | Single | Multiple
Scalable | No | Yes | Yes | Yes
Mechanical Design | 3-DOF | 2-DOF | 0-DOF | 2-DOF
Power Consumption | ≈ 100 mW | ≈ 23 W | ≈ 20 W | ≈ 11.65 W
Cost | ≈ 146 Euros | ≈ 35 Euros | ≈ 15 Euros | ≈ 20 Euros

Table 3.1: Comparison between the tested gripping systems

From the comparison table 3.1, we can observe that the optimal grasping mechanism in terms of hold strength vs. power consumption is the proposed 2-DOF gripper design as its payload requirements meet our criterion in the context of the MBZIRC 2020 challenge (Sec. 1.3.1).
The mechanical design of the gripper is reasonable and does not contain any unnecessary elements that add to the weight. The power consumption, though is greater than the EPM solution, is reasonable considering the decreased cost and increased grasping strength and is significantly lower than the power consumption of the UAV.

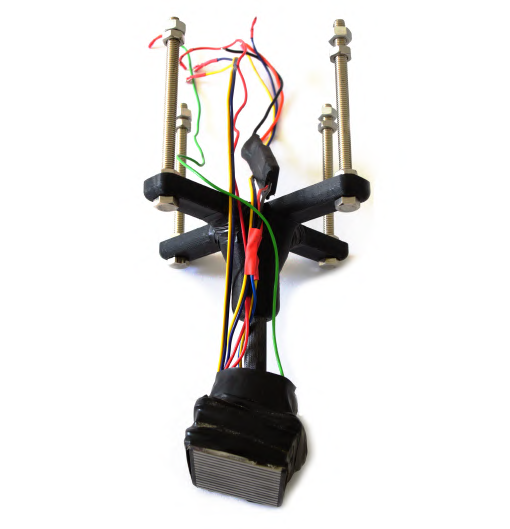
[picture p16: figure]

(a) gripper used for MBZIRC 2017 | (b) proposed gripper for MBZIRC
| 2020

Figure 3.9: Comparison between the previous gripper and proposed gripper

### 30 Chapter 3. Description of the Gripper

(a) Previously used EPM gripper grasping a 0.5 kg metal disk
(b) Proposed gripper grasping a 1.6 kg brick

Figure 3.10: Side by side comparison of the grippers in outdoor test flights

# Chapter 4

# Feedback and Control

### Contents

Reliably detecting whether a payload is actually grasped and onboard the UAV is one of the most crucial tasks for aerial grasping and manipulation.
There have been numerous works where the information about such payload coupling is estimated through the control of the drone wherein the controller detects the increase in the mass of the UAV system and compensates for this mass by varying thrust. Additionally, it is also possible to compensate for a swinging payload under the UAV and stabilize it through the controller [40][43][41]. This method however, becomes more challenging as the payload mass starts to become comparable with the UAV’s mass while considering that the UAV must actually grasp the brick for the controller to estimate the mass gradually and requires fine tuning to be practical enough to be employed in time constrained scenarios.

For our task, it is critical to know whether the brick has been successfully grasped almost immediately as the UAV has to fly the payload to the wall area without delay.
In case the grasp was unsuccessful, the UAV must try again to grasp the brick or decide to abandon the brick altogether. These decisions will be made on a higher level by a state machine that runs in the UAV’s onboard computer (Sec. 5.1). We shall discuss various sensing and estimation techniques for feedback to explore all possibilities and choose the optimal one for the purposes of our task.

### 32 Chapter 4. Feedback and Control

## 4.1 Feedback with ultrasonic sensors

The first sensor tested was the HC-SR04 ultrasonic sensor (Fig. 4.1 from [44]) with sensing range of 2 cm - 4 m and sensing accuracy of ± 3 mm¹
. Two sensors were tested with the first gripper prototype which had a longer body and hence was mounted on the sides of the long body as shown in Fig. 3.2.
The ultrasonic sensor works on 5 V which can by supplied from the Arduino and by a trigger and echo function. The trigger pin controls the transmitter which transmits ultrasonic pulses at 40 kHz for 10 microseconds and waits for the reflection after hitting an object and is then received by the receiver (Fig. 2.3).
The sensor then returns the duration it took and knowing the speed of sound in air, we can calculate the distance to the detected object (Eq. 2.3). During preliminary test flights,

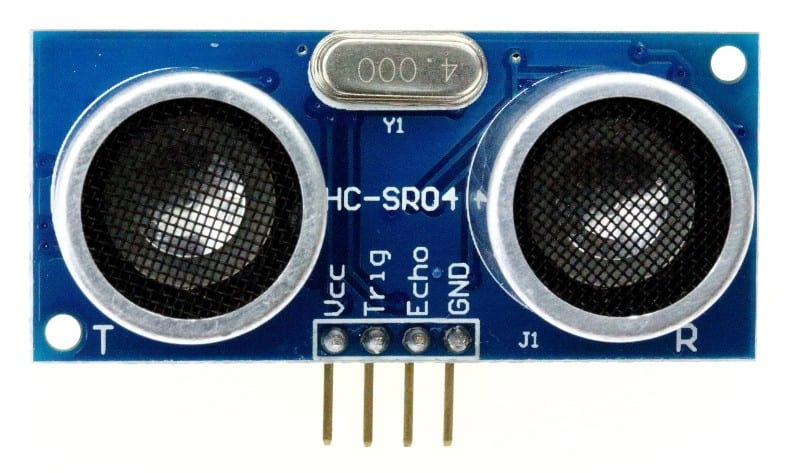
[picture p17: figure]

Figure 4.1: HC-SR04 ultrasonic sensor

it was observed that the raw distance data calculated from the sensors were too noisy to be used for accurate feedback. This was due to the fact that the ultrasonic sensor is not a good instrument to accurately measure distances onboard a flying UAV as the sensor itself has small delays due to the limitation of the speed of sound.
Nevertheless, we chose to prototype with the sensor because it was low cost, small-sized and could be used onboard the gripper easily. However, there are far better and more expensive ranging devices available on the market like the onboard laser based Garmin rangefinder² which is used by our UAV system for altitude measurements. As light based ranging techniques are much faster, it would be more suitable for applications onboard a UAV rather than the used ultrasonic sensor.
The noisy raw distance data from the sensors had to be filtered in order to get accurate distance data and feedback. The graphs (Fig. 4.3) and (Fig. 4.4) show the calculated distances from the sensors before and after median filtering with a window size of 20 samples.

1Sensor Data sheet - https://www.electroschematics.com/hc-sr04-datasheet/
2Garmin LIDAR-Lite V3 - https://buy.garmin.com/en-US/US/p/557294

4.1. Feedback with ultrasonic sensors | 33

The algorithm (Fig. 4.2) used for detection of successful grasping with an ultrasonic sensor is as follows.
The distance³
in cm is calculated from the ultrasonic sensor and a measurement of 20 samples are median filtered to produce a single final distance value. The median filter is a filter used to remove “out of range” noise from a signal as in the case with our ultrasonic sensor. The filter works by sliding through the signal using a window and replacing the neighbours in the window with the median of the neighbours. The window size for the median filter selected experimentally was 20 samples and implemented in the firmware of the Arduino.
Once the UAV grasps a brick, the drop (Fig. 4.3) (Fig. 4.4) in the distance at that instance is compared to a known threshold of 4 cm which is the minimum possible distance when the gripper touches a flat surface completely and hence was the minimum distance possible should the gripper grasp a brick.

Distance [cm] = ((duration [μs] / 2) * 0.0343)

Figure 4.2: Feedback algorithm using ultrasonic sensors

3The distance is given by the product of the duration taken for single side transmission multiplied by the speed of sound in air in cm/µs ≈ 0.0343

### 34 Chapter 4. Feedback and Control

Figure 4.3: Unfiltered distance data from ultrasonic sensor during test flight

Figure 4.4: Median filtered distance data from ultrasonic sensor during test flight

4.2. Feedback with hall-effect sensors | 35

## 4.2 Feedback with hall-effect sensors

The sensor tested was the honeywell SS-49e⁴
. An analog linear hall effect sensor which uses a linear sourcing output voltage set by the supply voltage and varies it in direct proportion to the strength of the magnetic field. The sensor works on 5 V supplied from the arduino and was embedded into the electromagnet’s surface for maximum sensitivity (Fig. 4.5).

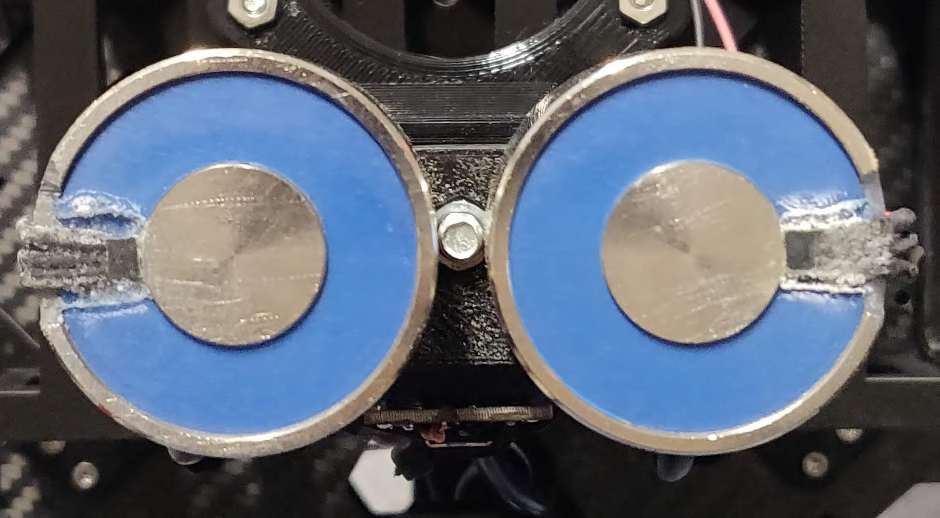
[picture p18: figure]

Figure 4.5: Hall sensors embedded in the electromagnet surface

The electromagnet, when powered, has a steady magnetic field provided that there are no parasitic fields in its close vicinity. When a ferrous object is grasped, this magnetic field is changed and the change is directly proportional to the thickness of the ferrous surface. By using the hall-effect sensor near the electromagnet, we can clearly detect this change in the magnetic field when a ferrous object is grasped.
The Arduino MCU does exactly that by measuring 50 samples and mean filtering them to smooth out the noise caused due any other magnetic anomalies. After filtering, a threshold is calculated and the final feedback is estimated by comparing the calculated threshold before the brick was grasped to the current measured value. In our particular case, there was a drop in the output voltage by the hall sensor when an object was grasped (Fig. 4.7).

The drawback with using this technique is that the hall sensor drifts due to the temperature variation caused by heating of the electromagnet and is easily affected by parasitic fields and requires to be calibrated by measuring some samples and mean filtering them before each grasp.

4SS49e Data sheet - https://sensing.honeywell.com/SS39ET-linear-and-angle-sensor-ics

### 36 Chapter 4. Feedback and Control

## 4.3 Feedback with inductive sensors

The inductive sensor used⁵
is an off the shelf industrial proximity sensor with 8 mm diameter and 5 cm height commonly used in 3D printers for sensing proximity to build plate. It is lightweight, noise resistant and easy to work with (Fig. 4.6 from [45]). It outputs a digital high signal when there is no ferrous object near its proximity and switches to a digital low signal when a ferrous object is bought near it. The feedback for the inductive

Figure 4.6: The used inductive proximity sensor

sensor is the most straight forward as it outputs a constant zero when a brick is grasped by the gripper (Fig. 4.8). The algorithm just checks if the feedback from the inductive sensor is zero and provides the feedback.
There were no major disadvantages using this sensor as it came with a noise filtering circuit out of the box and is widely used for industrial sensing of ferrous objects. However, the position of the sensor must be 2 mm or less from the surface of the ferrous brick to be grasped and in comparison with the hall sensors which have to be “embedded” into the magnet by modifying it, using the proximity sensor is easier. This was usually done while assembling the gripper in a one time calibration and to ensure that the sensor didn’t move during flight it was fixed in place using hot-glue.
Two different sensors with sensing distances of 8 mm and 2 mm were tested and the smaller proximity sensor with the sensing distance of 2 mm was found to be sufficient for our task as the sensor only required a one time position calibration.
The raw output from the hall-effect (Fig. 4.7) and inductive (Fig. 4.8) sensors and their corresponding feedback were obtained during experimental outdoor test flights.

5The sensor used is the LJ8A3-2-Z Inductive Proximity Sensor

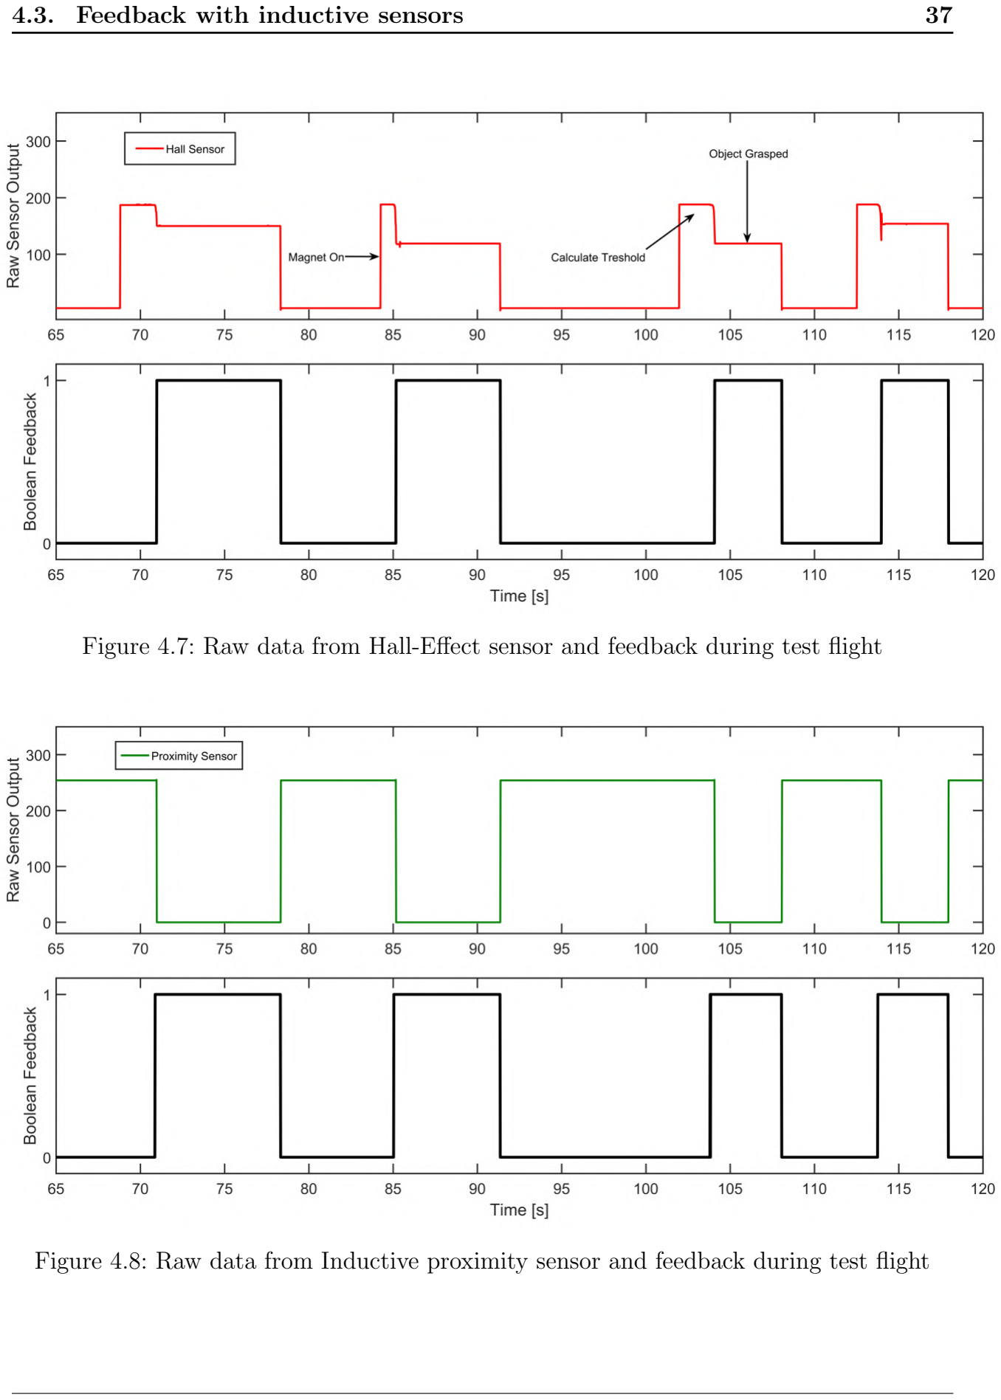
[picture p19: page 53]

4.3. Feedback with inductive sensors | 37

Figure 4.7: Raw data from Hall-Effect sensor and feedback during test flight

Figure 4.8: Raw data from Inductive proximity sensor and feedback during test flight

### 38 Chapter 4. Feedback and Control

## 4.4 Fusion of feedback methods

We have discussed the implementation and feedback technique for each of the sensors above and also their advantages. Nevertheless, a major drawback of using a single type of sensing technique is that if there is any interference or failure and the primary sensor system is compromised, it cripples the entire system’s ability to function as it was designed. As an example, a lot of aviation and robotic systems use redundant measurement or sensing techniques to ensure that the entire system can function properly even if some sensors fail or are compromised due to jamming or interference.

Using this concept as a motivation, we propose using a combination of the hall effect and inductive proximity sensor (Fig. 4.9) as together they provide the necessary redundancy required and estimate the feedback using two independent sensing techniques making the feedback obtained even more reliable. With our implementation, it is possible to obtain the combined feedback from both the sensors using OR logic to determine final feedback or feedback from any individual sensor and use it in ROS. Furthermore, there is diagnostic data with raw measurements and feedback states for easy fault detection and debugging. The estimation algorithm running onboard the MCU is shown in the flowchart Fig. 4.10.

Figure 4.9: Combined data from proximity & hall sensor and feedback during test flight

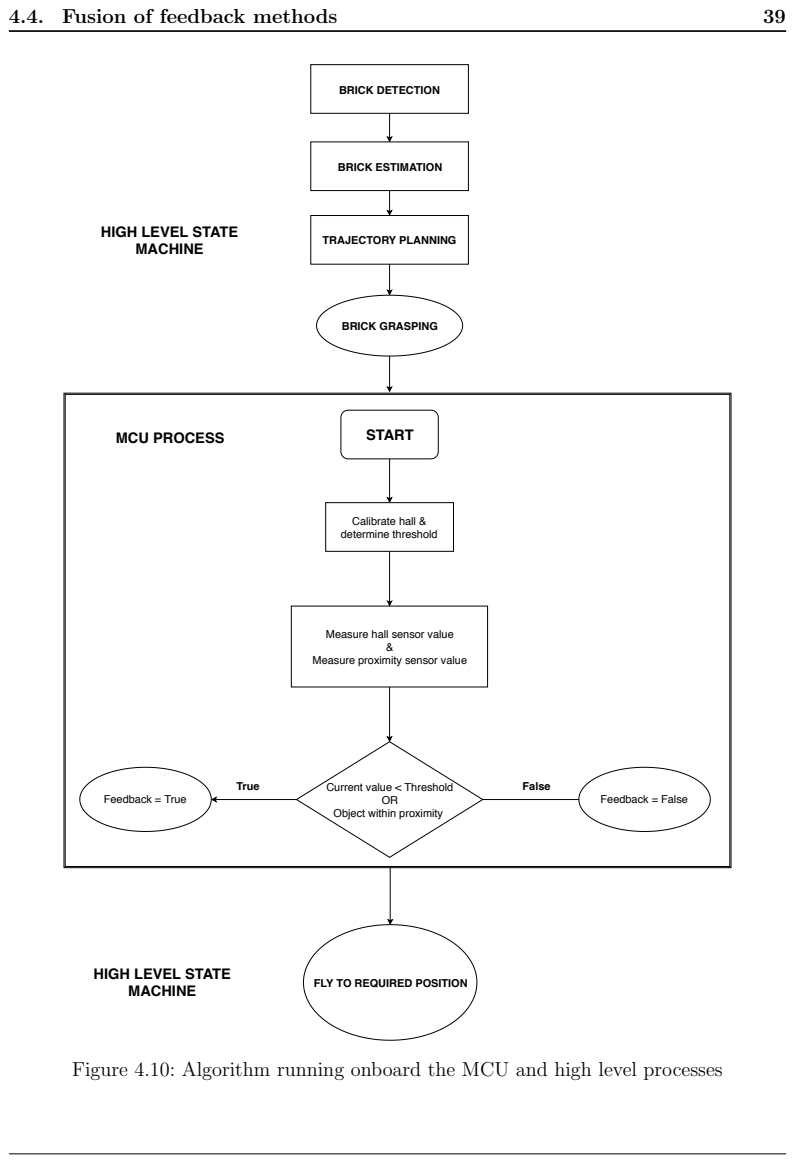
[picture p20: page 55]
4.4. Fusion of feedback methods; START; Calibrate hall & determine threshold; Feedback = True; True; False; MCU PROCESS; BRICK DETECTION; BRICK ESTIMATION; TRAJECTORY PLANNING; BRICK GRASPING; Feedback = False

HIGH LEVEL STATE
MACHINE

Measure hall sensor value

Measure proximity sensor value

Current value < Threshold

Object within proximity

FLY TO REQUIRED POSITION

Figure 4.10: Algorithm running onboard the MCU and high level processes

### 40 Chapter 4. Feedback and Control

## 4.5 Gripper control

### Control Circuit

The gripper is controlled with a help of a custom designed switching circuit [46] consisting of a N-MOSFET and protective flyback diode [30] that provides the switching action for the electromagnet by a digital signal from the MCU. For prototyping and for the purpose of this thesis, the Arduino MCU with an ATmega328 microprocessor is used for processing the signals from the sensors and providing the control of the electromagnets. But for the competition a custom designed STM 32 MCU board by the MRS group will be used that will provide all the necessary functions for the control and feedback processing of the gripper.

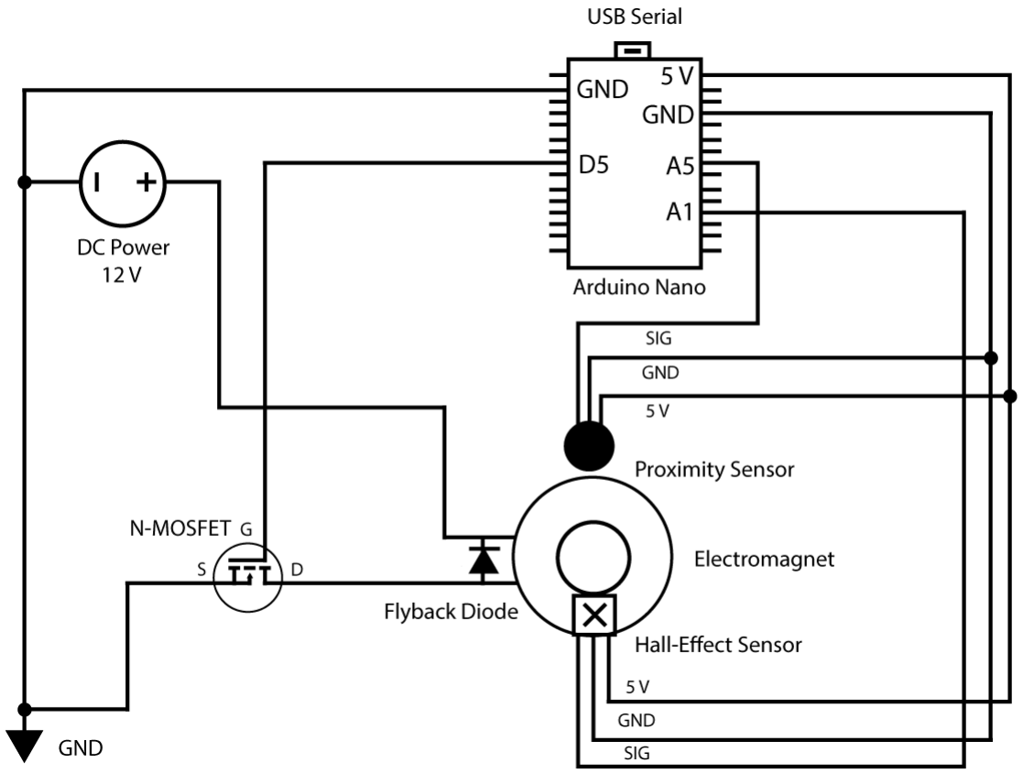
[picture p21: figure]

Figure 4.11: Electrical schematic of the gripper circuit

4.5. Gripper control | 41

### Serial communication

The communication between the gripper and the onboard computer on the UAV is facilitated by a custom “MRS Serial” protocol using an USB cable plugged into the onboard computer.
Messages transmitted and received via this protocol consist of 8-bit values following the rules of UART communication. The protocol is illustrated in Fig. 4.12.

Figure 4.12: Description of the serial protocol

Each character inside the box represents one 8 bit value. The first byte is always the character “b”, this represents the start of a serial message. The next byte written is the payload size. Payload of the message can range from 1 to 256 bytes long and the first byte of the payload is the message id, which is pre-defined and serves to differentiate between different messages of the same length. The message id is followed by the payload and finally, the checksum is calculated by the sender by summing the 8-bit data stream and compared at the receiving end. If the checksums do not match, the message is discarded. This is summarized in (table 4.1).

### 42 Chapter 4. Feedback and Control

Byte | function
b | Message start
Payload size | Size of the expected message
Message ID | Identifier that ensures messages are parsed correctly
Payload | Actual message
Checksum | Ensures messages are not corrupted or in-complete at the receiving end

Table 4.1: Serial bits and their function in used protocol

### ROS Node

A ROS node runs on the onboard computer and is integrated into the software pipeline of the UAV’s system. This node publishes diagnostic information about the gripper for easier debugging and also publishes the feedback from the gripper via ROS topics.
The gripper is controlled by ROS services that allows for the control of the electromagnet and also sensor calibration in the case of the hall sensor. A table of the functions provided by the ROS node and their message IDs for serial communication is shown below (table 4.2):
Name | Type | Purpose | Message ID
Grip | ROS Service | Turn the gripper ON and cali-brate onboard sensors | 0x40
Ungrip | ROS Service | Turn the gripper OFF | 0x41
gripper diagnostics | ROS topic | Provide diagnostic information from sensors such as raw values and gripper state | N/A
gripper feedback | ROS topic | Provide final boolean feedback | N/A

Table 4.2: Implemented functions facilitated by ROS

The switching control of the gripper is provided by two ROS services (Sec. 2.1) “grip” and “ungrip” which turns the electromagnet on and off respectively by providing a high or low signal to the MOSFET (table 4.2). The calibration of the hall sensor is done automatically when the “grip” ROS service is called which is performed by the state machine after an object is detected and the UAV descents to grasp it. The gripper diagnostics topic publishes information for debugging such as the current state of the gripper, the measured raw sensor values and feedback from the individual sensors. The gripper feedback provides a final estimation to the drone which is a boolean value.

# Chapter 5

# Outdoor Experiments

### Contents

In order to experimentally validate the proposed idea for an aerial grasping mechanism, we conducted a series of experiments 12 under both indoor and outdoor conditions where the UAV system for challenge II of MBZRIC 2020 along with the grasping mechanisms were tested thoroughly.
In this chapter, an overview of the entire system under development for the competition and the experimental data from the test flights are presented.

## 5.1 Overview of UAV system

### Hardware Architecture

The proposed UAV platform is a complex system with multiple onboard sensors and computational units shown in Fig. 5.1. The open-source nature of the system makes it ideal for rapid prototyping which in turn makes them perfect for competition scenarios and multi-robot system research.
The hardware components are selected with certain factors such as payload, reliable sensor data and computational power in mind. The UAV frame selected is the tarot 650 sport quad-copter with carbon fiber frame making it lightweight while satisfying the size requirements given for the MBZIRC 2020 competition.

1Autonomous grasping test: https://youtu.be/WBgUNp1UqlA
2Piloted grasping test: https://youtu.be/bOQ2FRhOzXw

### 44 Chapter 5. Outdoor Experiments

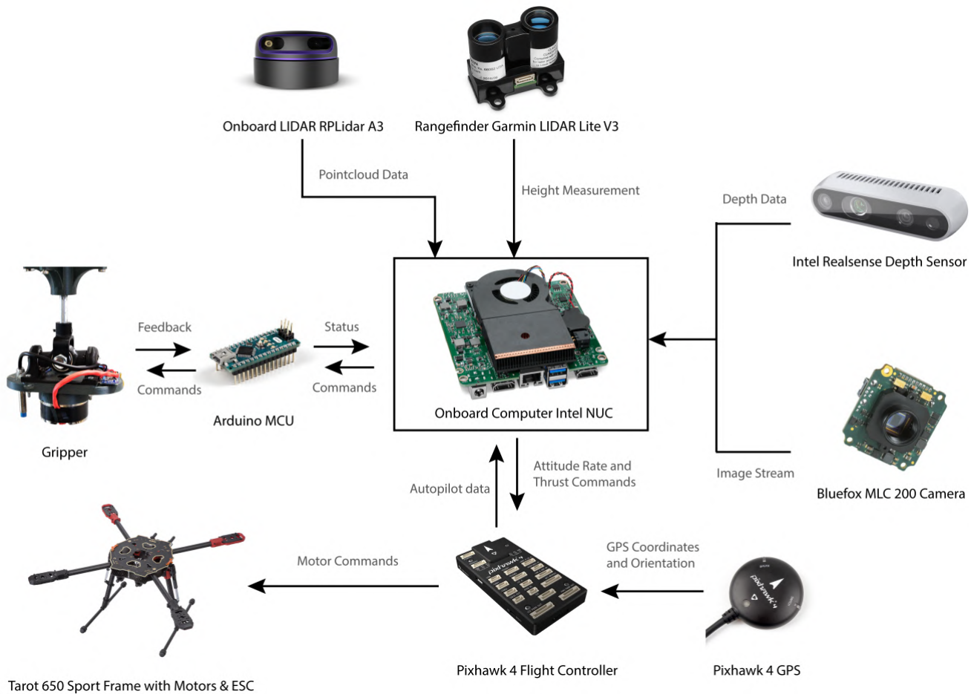
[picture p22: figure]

Figure 5.1: Hardware architecture

The system is controlled at the lowest level by a Pixhawk 4 flight controller with its own GPS that provides reliable coordinates and contains various sensors such as gyroscopes, accelerometers, magnetometers and barometer.
An Intel NUC-i7 computer provides the necessary computational power required to solve the image processing, signal processing, state estimation, feedback control, motion planning and UAV coordination tasks effectively. The communication between the computer and the Pixhawk controller is done with the MAVlink protocol and communication between the UAVs in a group is achieved with the help of the WIFI module on the NUC computer. Two Bluefox MLC 200 cameras are used for challenge II onboard the UAV, one running an optic flow [47] algorithm that provides odometry during navigation and the other fitted with a fisheye lens that provides a wider field of view in the detection for brick grasping [48] while the LIDAR is used for localization [16] of the UAV and mapping of the environment. The Intel realsense depth camera will be used conditionally if the task requires it, for example in the case of assembly of the wall in challenge II or in challenge III where a group of UAVs must extinguish a series of fires in a simulated urban fire-fighting scenario.

5.1. Overview of UAV system | 45

While the pixhawk controller provides barometric altitude readings, the UAV does not have any information about the distance to a detected brick or the ground from the pixhawk. This is solved by the garmin lite v3 rangefinder which provides distance to ground readings in realtime.
Finally, the gripper communicates information about the feedback status with the computer with the help of an Arduino nano MCU running a custom serial protocol described in (Sec. 4.5) and can be controlled via the serial protocol for grasp and release of an object.

### System Software Pipeline

The software used for the UAVs utilizes the open-source Robot Operating System (ROS) running on the Intel NUC computer in which each task and sub-tasks can be split into smaller manageable structures in ROS (Nodes). All software changes are rigorously tested in Gazebo simulator along with the firmware from Pixhawk as this provides a realistic test-bed for our systems minimizing crashes and increasing safety during field tests.

Figure 5.2: Overview of software pipeline

An overview of the system pipeline is illustrated in Fig. 5.2. The main core of the system consists of a state machine which is used to manage all sub-systems and asynchronously

### 46 Chapter 5. Outdoor Experiments

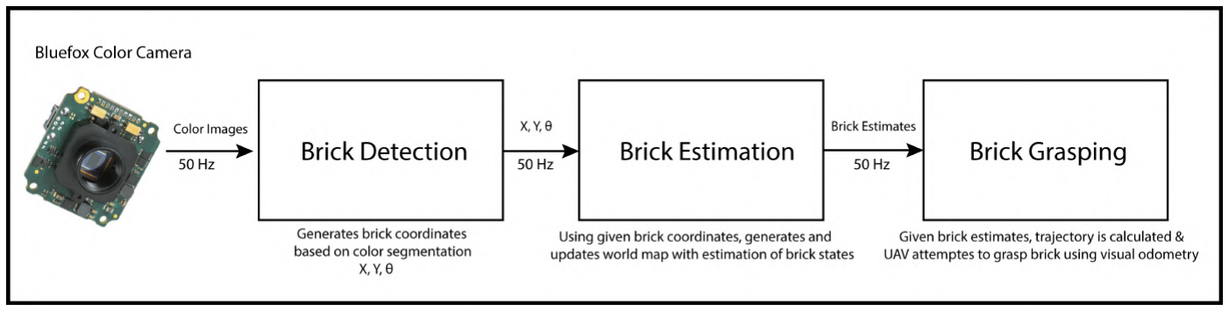
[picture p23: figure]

Figure 5.3: Sub-Pipeline for autonomous grasping

multiplexes between different sub-pipelines as required depending upon a particular task, which in our case corresponds to challenge II. The state machine is designed with the help of FlexBE (Python Library) and is fully integrated into the designed ROS system framework [49].

The state machine, in the first step is fed information from a brick placement scheduler which relays information about each brick object and its pre-defined parameters such as color, weight and priority. It also contains the order of how each brick must be placed in the wall as prescribed by a plan given to us before the challenge. The second step consists of the state machine performing various sweeps of the competition arena where individual bricks are detected, localized and the scheduler is updated accordingly.

The brick estimation and grasping sub-pipeline is illustrated in Fig. 5.3. As illustrated, the color camera searches the competition arena while running a brick detection algorithm that uses color segmentation [50][48] and navigates during flight on an optical flow algorithm using a grey-scale camera [47]. Once a brick is detected and localized the coordinates of the brick on the ground are calculated and relayed to the brick estimation algorithm which generates the map containing the brick states. The brick estimator keeps track of all the detected bricks in the environment and deactivates or deletes a brick if the grasping is unsuccessful or if the brick is already assembled on the wall.
Once the brick is estimated and trajectory leading to a particular brick is known, the UAV goes to the given coordinates using waypoints and aligns itself horizontally above the estimated position of the brick. It then descends to a height of 1.5 m above the ground. Once the UAV has reached the desired height and is aligned above the brick it tries to grasp the brick by turning on the gripper and descending gently onto the brick surface.
If the brick is successfully grasped the gripper returns positive detection and the UAV ascends to nominal height and flies to the wall-building area where each brick is assembled according to the brick layout map using a depth camera and visual servoing. If the UAV is unable to grasp the brick in 3 attempts, the state machine terminates the process with the outcome that grasping was unsuccessful.

5.1. Overview of UAV system | 47

On the low-level, the UAV is stabilized and controlled by the control pipeline [51] shown in Fig. 5.2. Automatic control of the UAVs relies on estimates of the states of the UAV model. The platform is equipped with multiple onboard sensors providing independent localization data and fuses this information to obtain a single and smooth estimate of UAV “pose” which contains both horizontal and vertical position, velocity estimation and is an important criteria as the non-linear SO(3) controller with state feedback is sensitive to noise [51].
The position controller uses the estimated state in a feedback loop to follow the trajectories given to it by the trajectory planner [49].
(a) UAV transporting red brick

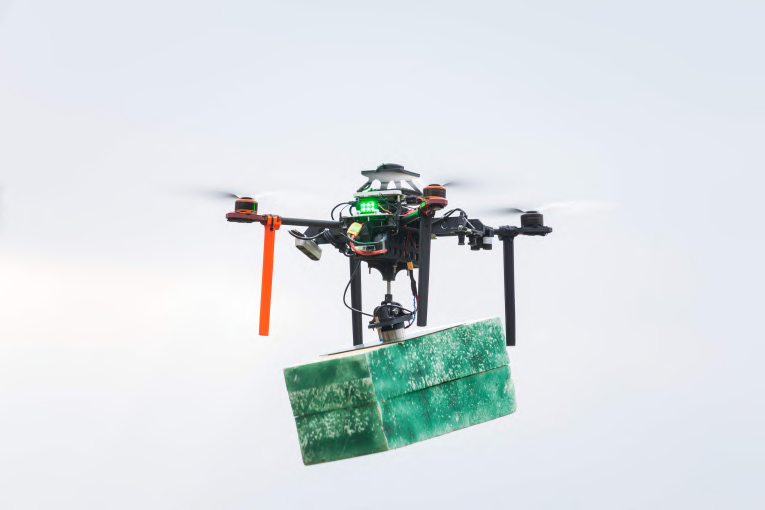
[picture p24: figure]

(b) UAV transporting green brick

Figure 5.4: The complete system in action during outdoor experimental flights

### 48 Chapter 5. Outdoor Experiments

## 5.2 Experimental data & observations

### Maximum Payload

Multiple experiments were conducted in the Czech countryside in experimental camps by the MRS group where the entire hardware and software system described (Sec. 5.1) was tested. The maximum payload grasped by the gripper system was 4 kg with nominal loads of 1.5 kg - 2 kg and excluding the UAV mass which was around 3 kg. The maximum payloads correspond to the blue and green bricks that are 1.2 m and 0.6 m long.
An important factor to consider is the payload limitations of the UAV system itself as even though the gripper is capable of theoretical payloads up to 6 kg, the first test conducted with the heaviest green brick resulted in a failure due to the low-pitch propellers that did not provide the necessary thrust for the mass of the entire system and had to be changed to propellers with a higher pitch angle which was then successful in lifting the heavier bricks.

### Maximum Sustainable Slide

Sudden aerial maneuvers and attitude change by the UAV during flight affect the forces on it’s payload and considering that the holding force of electromagnets are especially vulnerable to shear forces acting on it [52][16], we had to experimentally approximate the maximum sustainable slide forces for our grasping mechanism.
The selected electromagnet was tested with lateral pull tests with a weighing scale to measure at what point the payload would slide off the electromagnet. An important parameter here (table 5.1) is the thickness of the ferrous plate as this greatly affects the holding force of the electromagnet [33]. During flight, newton’s second law plays a major role in determining the forces acting on the payload during aggressive maneuvers. Therefore, the higher the mass of the payload, the more force acting on it. For the competition, we will restrict the UAV from making aggressive attitude changes and also limit the velocities of the UAV in order to ensure safety and reliability of operation. The experimentally tested values for the maximum sustainable slide are shown in table 5.1.
Brick Color | Plate Thickness | Mass | Max Sustainable Slide Force
Red | 0.75 mm | 0.75 kg | 0.87 kg
Green | 1.5 mm | 1.37 kg | 2.00 kg
Blue | 2.00 mm | 2.36 kg | 4.80 kg

Table 5.1: Test of maximum slide force

5.2. Experimental data & observations | 49

### Aerial Grasping

The final test we performed were direct grasp and release tests with the UAV and gripper system in both piloted and autonomous flights.
In order to measure the performance of the grasping system during autonomous flight, we took positional measurements when there was a payload attached to the UAV.
The graph (Fig. 5.6) shows the data calculated from the odometry of the UAV and the “setpoints” given to the UAV. By subtracting the real positional data from the set-point values, we can calculate the positional control error of the UAV during grasping and transport of the bricks. From (Fig. 5.7), we can observe that the set-point position error of the UAV during flight does not exceed 20 cm even with payload coupling. Taking into consideration that the UAV controller design is robust enough for such aerial grasping tasks, this is a good metric to measure the performance of our proposed grasping mechanism and show that it does not cause major disturbances to the UAV system.

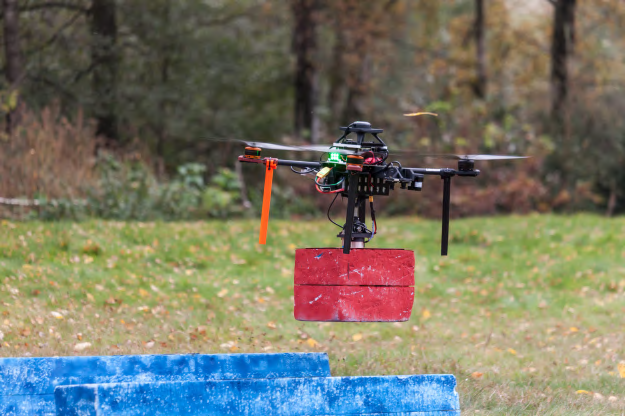
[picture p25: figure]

(a) The UAV hovers while placing the green brick (b) UAV flies above the wall with the red brick
(c) UAV grasps pliers showing the versatility of the
gripper
(d) UAV attempts to place the red brick on the wall

Figure 5.5: Snaps from outdoor experiments where the complete system is tested under the challenge II scenario

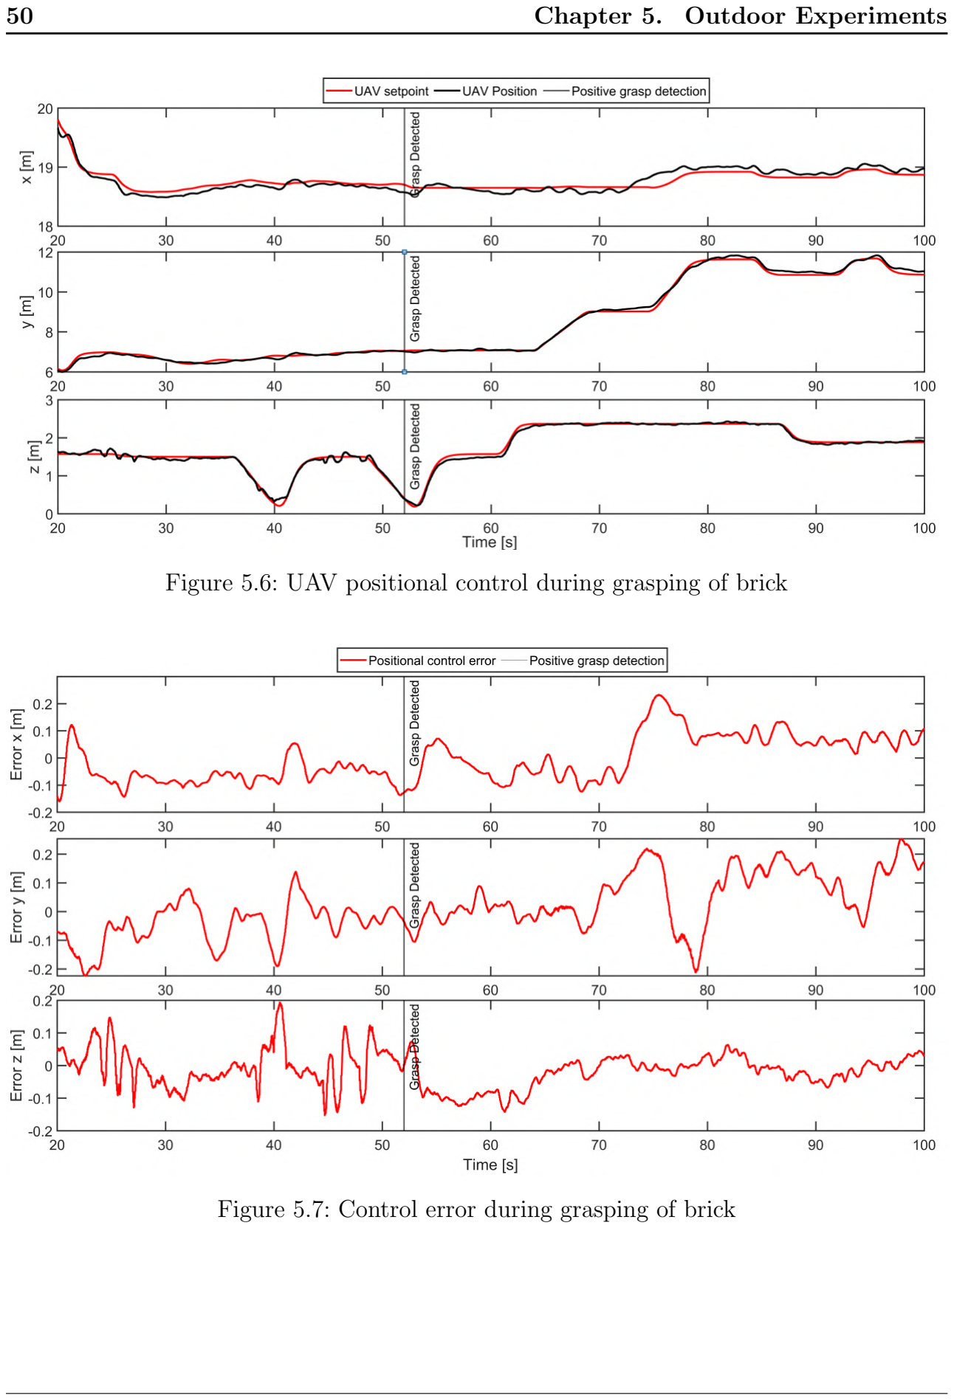
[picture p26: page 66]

### 50 Chapter 5. Outdoor Experiments

Figure 5.6: UAV positional control during grasping of brick

Figure 5.7: Control error during grasping of brick

# Chapter 6

# Conclusion

### Contents

In this thesis, we have developed a novel mechanism for aerial grasping and manipulation by autonomous unmanned aerial vehicles. The proposed final design of the grasping mechanism is a result of many iterations that were tested with test bricks in outdoor experimental test flights as well as indoor conditions. The final design was refined over time and is robust, reliable and has sufficient payload capabilities for a wide variety of ferromagnetic payloads.
An overall description of the UAV system in development for MBZIRC 2020 competition and the integration of the grasping mechanism with the system is also discussed. According to the formal assignment of this bachelor’s thesis, the following tasks have been completed:
- A novel magnetic based grasping mechanism has been designed and tested with real test bricks as per the MBZIRC 2020 requirements [See chapter 3].
- The feedback system consisting of various sensors was tested and a suitable system along with the estimation algorithm is implemented [See chapter 4].
- The implemented gripper system is integrated with ROS and communicates with the onboard computer to provide an estimate of the feedback status 4].
- Outdoor tests with real experimental data and evaluation of the tested systems are provided and discussed [See chapter 5].

### 52 Chapter 6. Conclusion

## 6.1 Future work

Autonomous aerial grasping by UAVs is becoming a widely studied topic in the field of aerial robotics. However, the current state of the art in UAV technologies is limited due to limitations in battery technology and onboard processing power. In the coming years, as battery technologies improve and more off the shelf products for aerial robotics emerge, UAVs will be more practical to employ for long-range tasks as well as aerial manipulation tasks of heavier payloads.

During the development of this thesis, several ideas were experimented with such as adding some actuation to the 2-DOF gripper using servos to align the payload toward the center of gravity and provide better stabilization or using springs for passive stabilization. Most of these ideas did not make it to the final presented work due to its impracticality, complexity or deviation from the assigned task.
The presented work can be improved upon by scaling it up for heavier payloads and by implementing a better estimation technique with fuzzy logic or advanced sensor fusion. It is also crucial to have orientation feedback of the payload after grasping it for designing robust flight controllers that are disturbance tolerant. However, this is a challenging task to solve in the real world. Several other innovative ideas can also be used to make the proposed design more robust such as using lighter and stronger materials (e.g. carbon fiber composites) for manufacturing as such materials ensure integrity for long-term uses. Nevertheless, electromagnetic based grasping technologies due to their versatility prove to be strong candidates for the future of UAV based aerial manipulation.

# Bibliography

[1] R. Ritz and R. D’Andrea, “Carrying a flexible payload with multiple flying vehicles,” in 2013 IEEE/RSJ International Conference on Intelligent Robots and Systems, Nov 2013, pp. 3465–3471.
[2] N. Michael, J. Fink, and V. Kumar, “Cooperative manipulation and transportation with aerial robots,” Autonomous Robots, vol. 30, no. 1, pp. 73–86, Jan 2011. [Online]. Available: https://doi.org/10.1007/s10514-010-9205-0
[3] G. Loianno and V. Kumar, “Cooperative transportation using small quadrotors using monocular vision and inertial sensing,” IEEE Robotics and Automation Letters, vol. 3, pp. 680–687, 2018.
[4] M. Becker and D. Sheffler, “Designing a high speed, stealthy, and payload-focused vtol uav,” in 2016 IEEE Systems and Information Engineering Design Symposium (SIEDS), April 2016, pp. 176–180.
[5] M. A. Ma’sum, M. K. Arrofi, G. Jati, F. Arifin, M. N. Kurniawan, P. Mursanto, and W. Jatmiko, “Simulation of intelligent unmanned aerial vehicle (uav) for military surveillance,” in 2013 International Conference on Advanced Computer Science and Information Systems (ICACSIS), Sep. 2013, pp. 161–166.
[6] J. Chudoba, M. Kulich, M. Saska, T. B´aˇca, and L. Pˇreuˇcil, “Exploration and mapping technique suited for visual-features based localization of mavs,” Journal of Intelligent & Robotic Systems., vol. 84, no. 1, pp. 351–369, 2016.
[7] T. Ozaslan, G. Loianno, J. Keller, C. J. Taylor, and V. Kumar, “Spatio-temporally smooth local mapping and state estimation inside generalized cylinders with micro aerial vehicles,” IEEE Robotics and Automation Letters, vol. 3, no. 4, pp. 4209–4216, Oct 2018.
[8] G. Loianno, J. Thomas, and V. Kumar, “Cooperative localization and mapping of mavs using rgb-d sensors,” in 2015 IEEE International Conference on Robotics and Automation (ICRA), May 2015, pp. 4021–4028.

### 54 Bibliography

[9] T. Tomic, K. Schmid, P. Lutz, A. Domel, M. Kassecker, E. Mair, I. L. Grixa, F. Ruess,
M. Suppa, and D. Burschka, “Toward a fully autonomous uav: Research platform for indoor and outdoor urban search and rescue,” IEEE Robotics Automation Magazine, vol. 19, no. 3, pp. 46–56, Sep. 2012.
[10] N. Michael, S. Shen, K. Mohta, Y. Mulgaonkar, V. Kumar, K. Nagatani, Y. Okada,
S. Kiribayashi, K. Otake, K. Yoshida, K. Ohno, E. Takeuchi, and S. Tadokoro, “Collaborative mapping of an earthquake-damaged building via ground and aerial robots,” Journal of Field Robotics, vol. 29, no. 5, pp. 832–841, 2012. [Online]. Available: https://onlinelibrary.wiley.com/doi/abs/10.1002/rob.21436
[11] A. Nedungadi and M. Saska, “Design of an active-reliable grasping mechanism for autonomous unmanned aerial vehicles,” J. Mazal, Ed. Springer, 2020, presented at Modelling and Simulation for Autonomous Systems and Accepted for publication in Springer Lecture Notes in Computer Science, 2020.
[12] “MBZIRC 2020,” see: Challenge II, Accessed: 2-9-2019. [Online]. Available: https://www.mbzirc.com/challenge/2020
[13] U. A. Fiaz, M. Abdelkader, and J. S. Shamma, “An intelligent gripper design for autonomous aerial transport with passive magnetic grasping and dual-impulsive release,” in 2018 IEEE/ASME International Conference on Advanced Intelligent Mechatronics (AIM), July 2018, pp. 1027–1032.
[14] J. Lee, D. H. Shim, S. Cho, H. Shin, S. Jung, D. Lee, and J. Kang, “A mission management system for complex aerial logistics by multiple unmanned aerial vehicles in mbzirc 2017,” Journal of Field Robotics, vol. 36, no. 5, pp. 919–939, 2019. [Online]. Available: https://onlinelibrary.wiley.com/doi/abs/10.1002/rob.21860
[15] A. R. Casta˜no, F. Real, P. Ram´on-Soria, J. Capit´an, V. Vega, B. C. Arrue,
A. Torres-Gonz´alez, and A. Ollero, “Al-robotics team: A cooperative multi-unmanned aerial vehicle approach for the mohamed bin zayed international robotic challenge,” Journal of Field Robotics, vol. 36, no. 1, pp. 104–124, 2019. [Online]. Available: https://onlinelibrary.wiley.com/doi/abs/10.1002/rob.21810
[16] G. Loianno, V. Spurny, T. Baca, J. Thomas, D. Thakur, T. Krajnik, A. Zhou, A. Cho,
M. Saska, and V. Kumar, “Localization, grasping, and transportation of magnetic objects by a team of mavs in challenging desert like environments,” IEEE Robotics and Automation Letters, vol. 3, no. 3, pp. 1576–1583, 2018.
[17] R. Bahnemann, M. Pantic, M. Popovic, D. Schindler, M. Tranzatto, M. Kamel,
M. Grimm, J. Widauer, R. Siegwart, and J. Nieto, “The eth-mav team in the mbz international robotics challenge,” Journal of Field Robotics, vol. 36, no. 1, pp. 78–103, 2019. [Online]. Available: https://onlinelibrary.wiley.com/doi/abs/10.1002/rob.21824

Bibliography | | | | 55
[18] A. Gawel, M. Kamel, T. Novkovic, J. Widauer, D. Schindler, B. P. von Altishofen,
R. Siegwart, and J. Nieto, “Aerial picking and delivery of magnetic objects with mavs,” in 2017 IEEE International Conference on Robotics and Automation (ICRA), May 2017, pp. 5746–5752.
[19] P. Kohout, “A system for autonomous grasping and carrying of objects by a pair of helicopters,” 2017, Master Thesis, Czech Technical University in Prague.
[20] R. Cano, C. P´erez, F. O. Prua˜no, A. Ollero, and G. Heredia, “Mechanical design of a 6-dof aerial manipulator for assembling bar structures using uavs,” in 2nd RED-UAS 2013 Workshop on Research, Education and Development of Unmanned Aerial Systems, 2013, pp. 1–7.
[21] G. Jiang and R. Voyles, “Hexrotor uav platform enabling dextrous interaction with structures-flight test,” in 2013 IEEE International Symposium on Safety, Security, and Rescue Robotics (SSRR), Oct 2013, pp. 1–6.
[22] M. Fumagalli, S. Stramigioli, and R. Carloni, “Mechatronic design of a robotic manipulator for unmanned aerial vehicles,” in 2016 IEEE/RSJ International Conference on Intelligent Robots and Systems (IROS), Oct 2016, pp. 4843–4848.
[23] P. E. I. Pounds, D. R. Bersak, and A. M. Dollar, “Practical aerial grasping of unstructured objects,” in 2011 IEEE Conference on Technologies for Practical Robot Applications, April 2011, pp. 99–104.
[24] C. C. Kessens, J. Thomas, J. P. Desai, and V. Kumar, “Versatile aerial grasping using self-sealing suction,” in 2016 IEEE International Conference on Robotics and Automation (ICRA), May 2016, pp. 3249–3254.
[25] D. Mellinger, Q. Lindsey, M. Shomin, and V. Kumar, “Design, modeling, estimation and control for aerial grasping and manipulation,” in 2011 IEEE/RSJ International Conference on Intelligent Robots and Systems, Sep. 2011, pp. 2668–2673.
[26] ROS, “ROS - Introduction,” accessed: 18-11-2019. [Online]. Available: http: //wiki.ros.org/ROS/Introduction
[27] Encyclopedia Britannica, inc., “Electromagnet,” accessed: 15-11-2019. [Online].
Available: https://www.britannica.com/science/electromagnet
[28] Binder Magnetic, “Technical explanations for holding magnets: Electromagnetic holding magnets,”
accessed: | 15-11-2019. | [Online]. | Available: | https://www.binder-magnetic.com/
documentation/technical-explanations-for-holding-magnets/?lang=en (https://www.binder-magnetic.com/documentation/technical-explanations-for-holding-magnets/?lang=en)
[29] Kendrion, “Technical definitions: The holding magnet,” accessed: 15-11-2019.
[Online]. | Available: | https://www.kendrion.com/industrial/ims/fr/competences/
technical-explaination/the-holding-magnet.html (https://www.kendrion.com/industrial/ims/fr/competences/technical-explaination/the-holding-magnet.html)

### 56 Bibliography

[30] T. Agarwal, “Flyback diode,” accessed: 15-11-2019. [Online]. Available: https: //www.elprocus.com/freewheeling-or-flyback-diode-circuit-working-functions/
[31] Kendrion, “Technical definitions: The electromagnet,” accessed: 27-11-2019.
[Online]. | Available: | https://www.kendrion.com/industrial/ims/en/competences/
technical-explaination/the-electromagnet.html (https://www.kendrion.com/industrial/ims/en/competences/technical-explaination/the-electromagnet.html)
[32] Wikipedia, “Remanence,” accessed: 27-10-2019. [Online]. Available: https://en.wikipedia.org/wiki/Remanence (https://en.wikipedia.org/wiki/Remanence)
[33] Goudsmit Magnetics, “Goudsmit - hold-force curve with plate thickness,” accessed: 15-11-2019. [Online]. Available: https://www.goudsmitmagnets.com/data/repository/documents/Forces GM17804.pdf (https://www.goudsmitmagnets.com/data/repository/documents/Forces_GM17804.pdf)
[34] Innover Bot, “Hc-sr04 ultrasonic sensor,” accessed: 12-26-2019. [Online]. Available: https://www.rima-technology.com/2017/07/23/ultrasonic-sensor-hc-sr04-arduino/
[35] Electro Schematics, “Inductive proximity working,” accessed: 12-26-2019. [Online]. Available: https://www.electroschematics.com/inductive-proximity-switch-w-sensor/
[36] Electronics Tutorials, “Hall effect sensor working principles,” accessed: 12-23-2019. [Online]. Available: https://www.electronics-tutorials.ws/electromagnetism/hall-effect.html (https://www.electronics-tutorials.ws/electromagnetism/hall-effect.html)
[37] P. Jaiswal, “Demystifying drone dynamics!” accessed: 21-11-2019. [Online]. Available: https://towardsdatascience.com/demystifying-drone-dynamics-ee98b1ba882f
[38] U.S. Department of Transportation (FAA), “Helicopter flying handbook,” see:
Chapter | 02 | - | Aerodynamics | of | flight, | Accessed: | 22-11-2019. | [Online].
Available: | https://www.faa.gov/regulations policies/handbooks manuals/aviation/
helicopter flying handbook/ (https://www.faa.gov/regulations_policies/handbooks_manuals/aviation/helicopter_flying_handbook/)
[39] NASA Glenn Research Center, “Beginner’s guide to aerodynamics,” see: Description of lift, Accessed: 12-23-2019. [Online]. Available: https://www.grc.nasa.gov/www/k-12/airplane/lift1.html (https://www.grc.nasa.gov/www/k-12/airplane/lift1.html)
[40] B. Lee, H. Lee, D. Yoo, G. Moon, D. Lee, Y. Kim, and M. Tahk, “Study on payload stabilization method with the slung-load transportation system using a quad-rotor,” in 2015 European Control Conference (ECC), July 2015, pp. 2097–2102.
[41] M. Bernard, K. Kondak, and G. Hommel, “A slung load transportation system based on small size helicopters,” in Autonomous Systems – Self-Organization, Management, and Control, B. Mahr and S. Huanye, Eds. Dordrecht: Springer Netherlands, 2008, pp. 49–61.

Bibliography | | | | | | 57
[42] P. Kirienko, “Opengrab epm v3 knowledge base,” see: Safety note under mechanical properties, Accessed: 12-10-2019. [Online]. Available: https://kb.zubax.com/display/MAINKB/OpenGrab+EPM+v3 (https://kb.zubax.com/display/MAINKB/OpenGrab+EPM+v3)
[43] Y. Feng, C. A. Rabbath, and C.-Y. Su, Modeling of a Micro UAV with Slung Payload. Dordrecht: Springer Netherlands, 2015, pp. 1257–1272. [Online]. Available: https://doi.org/10.1007/978-90-481-9707-1 108
[44] Robot Shop, “Hc-sr04 ultrasonic sensor working,” accessed: 12-16-2019. [Online]. Available: https://www.robotshop.com/uk/hc-sr04-ultra01-ultrasonic-range-finder. html (https://www.robotshop.com/uk/hc-sr04-ultra01-ultrasonic-range-finder.html)
[45] TSKTECH, “Inductive proximity sensor,” accessed: 12-16-2019. [Online]. Available: https://www.amazon.in/INDUCTIVE-PROXIMITY-SENSORS-SWITCH-Printer/dp/B07BJHXMBB (https://www.amazon.in/INDUCTIVE-PROXIMITY-SENSORS-SWITCH-Printer/dp/B07BJHXMBB)
[46] Electronics-Tutorials, “Mosfet as a switch,” accessed: 12-12-2019. [Online]. Available: https://www.electronics-tutorials.ws/transistor/tran 7.html
[47] V. Walter, T. Nov´ak, and M. Saska, “Self-localization of unmanned aerial vehicles based on optical flow in onboard camera images,” in Modelling and Simulation for Autonomous Systems, J. Mazal, Ed. Cham: Springer International Publishing, 2018, pp. 106–132.
[48] P. Stepan, T. Krajnik, M. Petrlik, and M. Saska, “Vision techniques for on-board detection, following, and mapping of moving targets,” Journal of Field Robotics, vol. 36, no. 1, pp. 252–269, 2019. [Online]. Available: https: //onlinelibrary.wiley.com/doi/abs/10.1002/rob.21850
[49] V. Spurny, T. Baca, M. Saska, R. Penicka, T. Krajnik, J. Thomas, D. Thakur,
G. Loianno, and V. Kumar, “Cooperative Autonomous Search, Grasping and Delivering in a Treasure Hunt Scenario by a Team of UAVs,” Journal of Field Robotics, vol. 36, no. 1, pp. 125–148, 2019.
[50] T. Baca, P. Stepan, and M. Saska, “Autonomous landing on a moving car with unmanned aerial vehicle,” in The European Conference on Mobile Robotics (ECMR), 2017.
[51] T. Baca, D. Hert, G. Loianno, M. Saska, and V. Kumar, “Model predictive trajectory tracking and collision avoidance for reliable outdoor deployment of unmanned aerial vehicles,” in 2018 IEEE/RSJ International Conference on Intelligent Robots and Systems (IROS), Oct 2018, pp. 6753–6760.
[52] Supermagnete, | “Shear | force | on | magnet | faqs,” | accessed:
12-19-2019. | [Online]. | Available: | https://www.supermagnete.de/eng/faq/
Why-does-my-magnet-not-carry-the-maximum-weight-on-the-wall (https://www.supermagnete.de/eng/faq/Why-does-my-magnet-not-carry-the-maximum-weight-on-the-wall)

### 58 Bibliography

# Appendices

# CD Content

In Table 1 are listed names of all root directories on CD.

Directory name Description
thesis | This thesis in PDF format
thesis source | Latex source code and figures used
source codes | Latest version of the gripper firmware running on the
| MCU and the ROS node
models | STL/design files of gripper for 3D printing
videos | videos of conducted experiments

Table 1: CD Content

62

# List of abbreviations

In Table 2 are listed abbreviations used in this thesis.

Abbreviation Meaning
ADC | Analog-Digital Converter
COTS | Commercial Over the Shelf
DC | Direct Current
DOF | Degree of Freedom
EPM | Electro-Permanent Magnet
ESC | Electronic Speed Controller
GPS | Global Positioning System
IDE | Integrated Development Environment
I/O | Input/Output
LIDAR | Light Detection and Ranging
MBZIRC | Mohammed Bin Zayed International Robotics Challenge
MCU | Microcontroller Unit
MRS | Multi-Robot System
MOSFET | Metal Oxide Semiconductor Field Effect Transistor
RPM | Revolutions Per Minute
ROS | Robot Operating System
UART | Universal Asynchronous Receiver-Transmitter
UAV | Unmanned Aerial Vehicle
UGV | Unmanned Ground Vehicle
USB | Universal Serial Bus
WIFI | Wireless Fidelity
VTOL | Vertical Take-Off & Landing

Table 2: Lists of abbreviations

### 64 Appendix . List of abbreviations

65

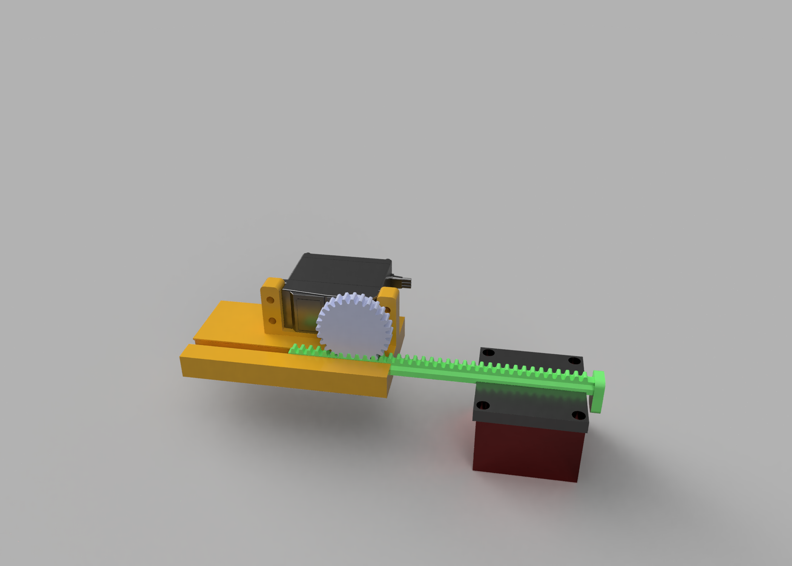
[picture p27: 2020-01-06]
videos/supplementry_media/A.Rejected_Designs/Linear_acutated_gripper_concept.png

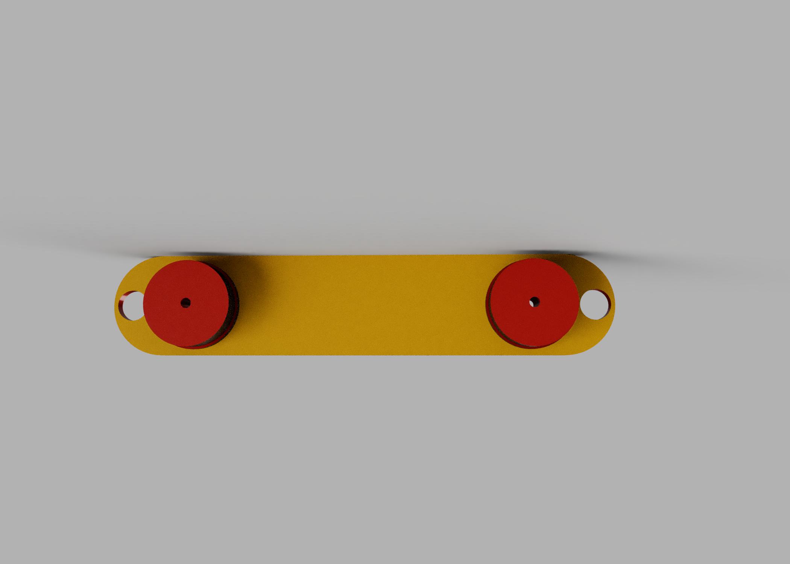
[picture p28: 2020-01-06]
videos/supplementry_media/A.Rejected_Designs/Dual_gripper_render.jpg

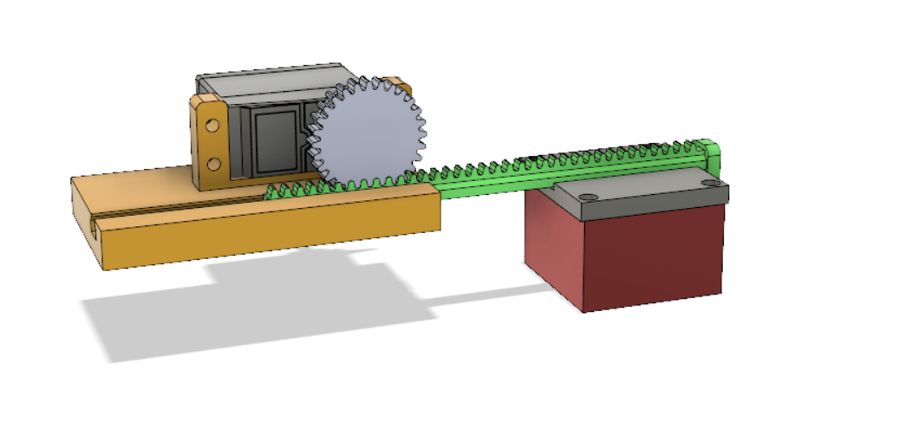
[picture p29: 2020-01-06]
videos/supplementry_media/A.Rejected_Designs/LAG_concept2.PNG

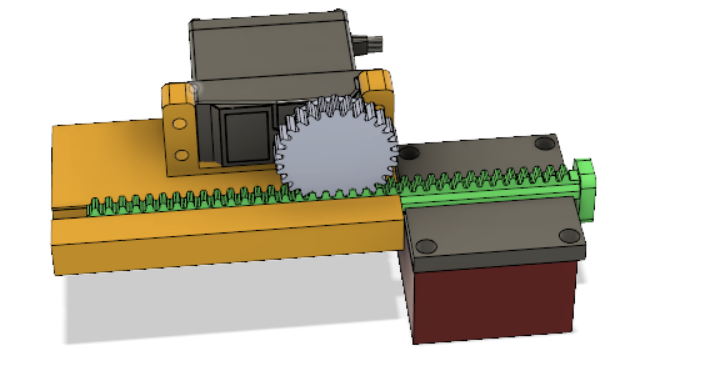
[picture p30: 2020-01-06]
videos/supplementry_media/A.Rejected_Designs/LAG_concept3.PNG

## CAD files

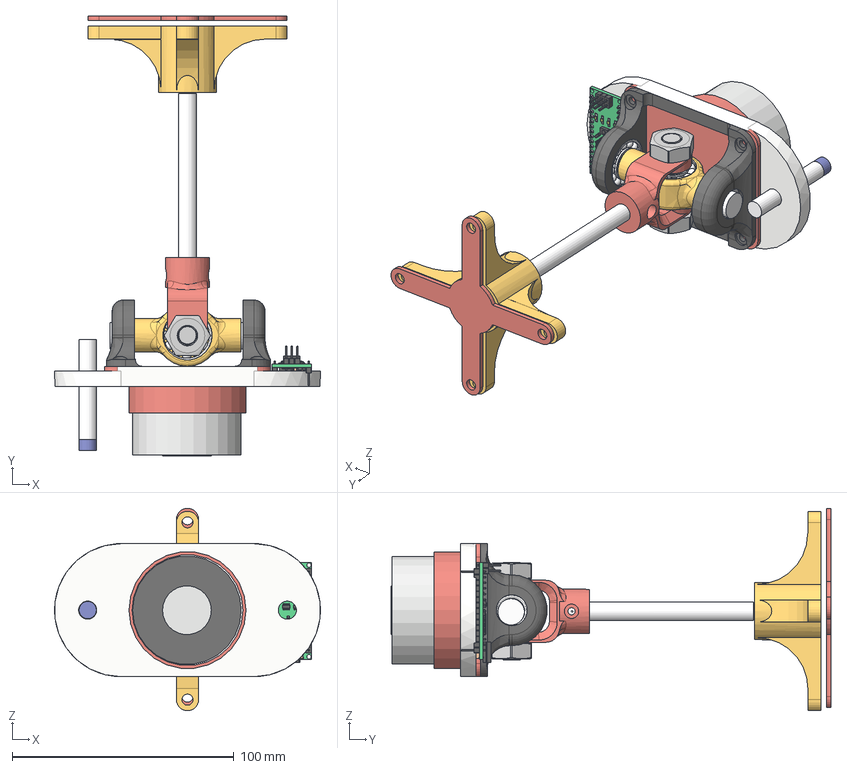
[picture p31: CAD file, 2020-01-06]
models/Gripper Assembly .step
120.0 x 198.4 x 91.3 mm
switch
Led x 3
Led (1)
Pin x 21
chip1
USB
Crystal
Pin (1) x 15
Res x 5
cap x 2
Chip
respack x 2
diode
vreg
Gripper Base v10
innerRing v1
magnets v1
Rod
heli v1
top v1
Ball Bearing 1 x 4
Hex Nut x 2
Prox Sensing Surface
49/21 Electromagnet
Threaded Coupler
Ring Coupler 2
Ring Coupler 1

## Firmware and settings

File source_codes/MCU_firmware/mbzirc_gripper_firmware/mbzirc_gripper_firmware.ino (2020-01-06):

// Define Right Sensor Pins Here
#define ProximitySensor 5      
#define HallSensor 1
#define MagPin 5    // MOSFET Pin Controlling Electromagnet

#define ProximitySamples 20   // Define Samples for Average Filter
#define HallSamples 50

int ProximityRaw;
int HallRaw;

int HallFeedback;            
int ProximityFeedback;

int Threshold;

bool MagFlag;                 // Flag for gripper state

void setup()
{
  
  Serial.begin (115200);
  pinMode (ProximitySensor, OUTPUT) ;
  pinMode (HallSensor, OUTPUT) ;
  pinMode (MagPin, OUTPUT);
  digitalWrite(MagPin, LOW);
}

void DebugWink()
{ 
  // Blinks LED - Used for Debuging Only
  for (int i = 0; i < 5; i++)
  {
    digitalWrite(13, HIGH);
    delay(1000);
    digitalWrite(13, LOW);
    delay(1000);
  }
}

void ResetHallThreshold()
{
  Threshold = 0;
}

void HallCalibrate()
// Calibrates Hall Sensor
{
  
  int HallAvg = 0;
  int SensorVal;
 
  for (int i = 0; i < HallSamples; i++)
  {
    SensorVal = analogRead(HallSensor);
    HallAvg = HallAvg + SensorVal;
  }

  Threshold = abs(HallAvg / HallSamples);
  
}


void EstimateFeedback()
{
  int PRaw, HRaw;
  
  ProximityRaw = 0;
  HallRaw = 0;


  //--------------------------PROXIMITY--------------------------------/
  for (int p = 0; p < ProximitySamples; p++)
  {
    PRaw = analogRead(ProximitySensor);
    ProximityRaw = ProximityRaw + PRaw;
  }
  ProximityRaw = abs(ProximityRaw / ProximitySamples);  // Average Samples
  
  //---------------------------HALL-----------------------------------/
  for (int h = 0; h < HallSamples; h++)
  {
    HRaw = analogRead(HallSensor);
    HallRaw = HallRaw + HRaw;
  }
  HallRaw = abs(HallRaw / HallSamples);

  // Feedback
  //------------------------------------------------------------------/
  if (ProximityRaw < 500)
  {
    ProximityFeedback = 1;
  }
  else
  {
    ProximityFeedback = 0;
  }
  //------------------------------------------------------------------/
  if (HallRaw < Threshold)
  {
    HallFeedback = 1;
  }

  else
  {
    HallFeedback = 0;
  }


}


void GripperProtocol(int ProxRaw, int HallRaw, int ProxFeedback, int HallFeedback, bool TotalFeedback, bool Flag)
{

  uint8_t crc = (uint8_t) 'b';
  uint8_t payload_size = 7;

  byte bytes[6];

  bytes[0] = ProxRaw;        // Raw Prox Data
  bytes[1] = HallRaw;        // Raw Hall Data

  bytes[2] = ProxFeedback;   // Feedback Estimate from Inductive Proximity Sensor
  bytes[3] = HallFeedback;   // Feedback Estimate from Hall Sensor
  
  bytes[4] = TotalFeedback;  // Total Feedback Estimate

  bytes[5] = Flag;           // Magnet State  

  bytes[6] = 0x23;           // EndMessage
    
  Serial.write('b');
  Serial.write(payload_size + 1); // Add a byte for Message ID

  // Write Data on Serial
  Serial.write(0x43);        // Message ID "32" - Used to distinguish msg from gripper vs. other instruments that use same protocol
  Serial.write(bytes[0]);    // Raw Feedback Proxmity Sensor
  Serial.write(bytes[1]);    // Raw Feedback Hall Sensor
  Serial.write(bytes[2]);    // Estimated Feedback Proximity Sensor
  Serial.write(bytes[3]);    // Estimated Feedback Hall Sensor
  Serial.write(bytes[4]);    // Total Estimated Feedback
  Serial.write(bytes[5]);    // Magnet State
  Serial.write(bytes[6]);    
  
  crc += 0x43 + payload_size + 1 + (uint8_t) bytes[0] + (uint8_t) bytes[1] + (uint8_t) bytes[2] + (uint8_t) bytes[3] + (uint8_t) bytes[4] + (uint8_t) bytes[5] + (uint8_t) bytes[6];
  Serial.write(crc);

  // Debug Msg
  //Serial.println((String)"b"+payload_size+bytes[0]+bytes[1]+bytes[2]+bytes[3]+bytes[4]+bytes[5]+bytes[6]+crc);
}

uint8_t Ash_Read_Single()
{
  if (Serial.available() > 3)
  {

    uint8_t crc = 0;
    uint8_t tmp_in;
    uint8_t cmd;
    
    tmp_in = Serial.read();

    // Message Start
    if (tmp_in == 'b')
    {
      crc += tmp_in;
      tmp_in = Serial.read();
      crc += tmp_in;
      
      tmp_in = Serial.read();
      cmd = tmp_in;

      crc += tmp_in;
      if (crc == Serial.read())
      {
        return cmd;
      }
    }
  }
  return 255;
}

void Switch_Mags(bool state)
// Function to operate the MOSFET Controlling Electromagnet
{
  
  if (state == true)
  {
    digitalWrite(MagPin, HIGH); // Turning on Electromagnet
    delay(10);
    MagFlag = true;
  }

  if (state == false)
  {
    digitalWrite(MagPin, LOW); // Turning off Electromagnet
    delay(10);
    MagFlag = false;
  }
}

void loop()
{
  // Read from Serial
  uint8_t mag_state = Ash_Read_Single(); 

  // Function to Toggle Magnets Based on Incoming Message
  if (mag_state == 0x40)
  {
    Switch_Mags(true); 
    
    HallCalibrate();
    delay(50);
    HallCalibrate();
   
  }
  else if (mag_state == 0x41)
  {
    Switch_Mags(false);
    
    HallCalibrate();
    delay(5);
    HallCalibrate();
    delay(5);
  }


  EstimateFeedback();
  GripperProtocol(ProximityRaw, HallRaw, ProximityFeedback, HallFeedback, (ProximityFeedback || HallFeedback), MagFlag);

}
